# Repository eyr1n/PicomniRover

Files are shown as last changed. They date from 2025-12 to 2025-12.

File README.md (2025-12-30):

# PicomniRover サポートリポジトリ

## 目次

- [これは何？](#これは何)
- [購入するものリスト](#購入するものリスト)
  - [秋月電子通商で購入可能なもの](#秋月電子通商で購入可能なもの)
  - [ロボットショップで購入可能なもの](#ロボットショップで購入可能なもの)
  - [モノタロウで購入可能なもの](#モノタロウで購入可能なもの)
- [3Dプリント部品について](#3dプリント部品について)
- [基板について](#基板について)
- [ライセンス](#ライセンス)

## これは何？

本リポジトリは、コミックマーケット107にて頒布した「やる気出ないんズ 活動報告書 vol.1」内の「かんたん！全方位移動ロボットのつくりかた」にて製作する全方位移動ロボット「PicomniRover」に関する情報をまとめたリポジトリです。

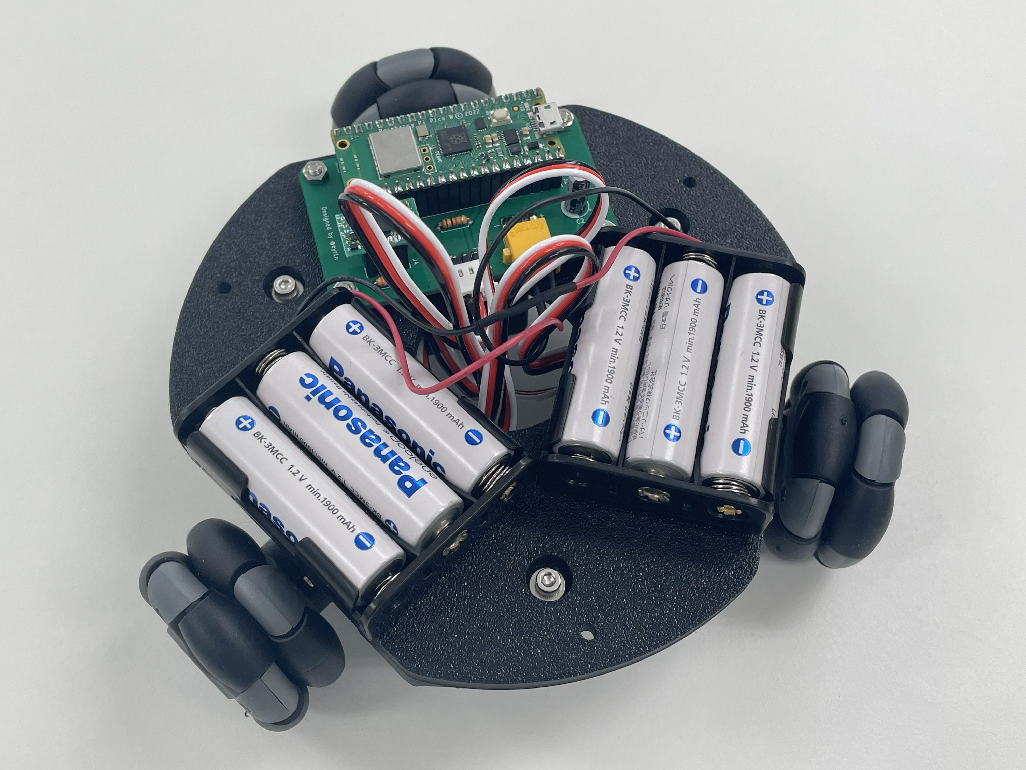
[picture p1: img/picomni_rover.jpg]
PicomniRover


## 購入するものリスト

ここでは、購入する必要のある市販の部品についてまとめます。私が使用した購入先は以下の3つです。

- [秋月電子通商 - https://akizukidenshi.com/](https://akizukidenshi.com/)
- [ロボットショップ(ヴイストン) - https://www.vstone.co.jp/robotshop/](https://www.vstone.co.jp/robotshop/)
- [モノタロウ - https://www.monotaro.com/](https://www.monotaro.com/)

すべてオンライン購入を前提に記載していますが、ねじ類などは近所のホームセンターでも代替可能です。必要に応じて入手しやすい手段を選んでいただければと思います。

また、同人誌内で製作するロボットの動作には、単3形の充電式ニッケル水素電池(公称1.2V)が6本必要です。Panasonic製eneloopやSony製CycleEnergyなど、単3形で公称電圧1.2Vの充電式ニッケル水素電池を用意してください。1.5Vのアルカリ乾電池は使用しないでください。

### 秋月電子通商で購入可能なもの

| 商品名 | 数量(使用数) | 単価(購入単位) | 購入リンク |
| --- | --- | --- | --- |
| Raspberry Pi Pico W | 1個 | ¥1,200 | [リンク](https://akizukidenshi.com/catalog/g/g117947) | 
| BNO055使用 9軸センサーフュージョンモジュールキット/AE-BNO055-BO | 1個 | ¥2,450 | [リンク](https://akizukidenshi.com/catalog/g/g116996) | 
| FEETECHシリアルバスサーボ STS3215 7.4V 14.4kg・cm 1:147 | 3個 | ¥2,780 | [リンク](https://akizukidenshi.com/catalog/g/g131132) | 
| 超高効率DCDCコンバーター(3.3V 0.5A) M78AR033-0.5 | 1個 | ¥380 | [リンク](https://akizukidenshi.com/catalog/g/g107178) | 
| 電池ボックス 単3×3本 リード線/BH-331-3A | 2個 | ¥70 | [リンク](https://akizukidenshi.com/catalog/g/g102667) | 
| XT30コネクター オス 基板取付用 XT30PW-M | 1個 | ¥70 | [リンク](https://akizukidenshi.com/catalog/g/g117949) | 
| XT30コネクター メス XT30U-F | 1個 | ¥50 | [リンク](https://akizukidenshi.com/catalog/g/g117950) | 
| Pch MOSFET 2SJ496TZ-E (60V 5A) | 1個 | ¥90 | [リンク](https://akizukidenshi.com/catalog/g/g109040) | 
| 電解コンデンサー 100μF 25V 105℃ ルビコンPX/25PX100MEFC5X11 | 1個 | ¥10 | [リンク](https://akizukidenshi.com/catalog/g/g117877) | 
| 積層セラミックコンデンサー 3.3μF 50V X7R 5mm/RDER71H335K3K1H03B | 1個 | ¥50 | [リンク](https://akizukidenshi.com/catalog/g/g108153) | 
| カーボン抵抗(炭素皮膜抵抗) 1/4W 1kΩ/CF25J1KB | 1本 (100本/袋) | ¥100 | [リンク](https://akizukidenshi.com/catalog/g/g125102) | 
| カーボン抵抗(炭素皮膜抵抗) 1/4W 3.3kΩ/CF25J3K3B | 2本 (100本/袋) | ¥140 | [リンク](https://akizukidenshi.com/catalog/g/g125332) | 
| ピンヘッダー 1×40 (40P)/PH-1x40SG | 2個 | ¥35 | [リンク](https://akizukidenshi.com/catalog/g/g100167) | 
| ピンヘッダー (L型) 1×6 (6P)/PH-1X6RG(2) | 1個 | ¥10 | [リンク](https://akizukidenshi.com/catalog/g/g105336) | 
| 分割ロングピンソケット 1×42 (42P)/FHU-1x42SG | 2個 | ¥80 | [リンク](https://akizukidenshi.com/catalog/g/g105779) | 
| 合計 |  | ¥13,260 |  | 

### ロボットショップで購入可能なもの

| 商品名 | 数量(使用数) | 単価(購入単位) | 購入リンク |
| --- | --- | --- | --- |
| 48mmオムニホイール(六角ハブ対応)(14038) | 3個 | ¥715 | [リンク](https://www.vstone.co.jp/robotshop/index.php?main_page=product_info&products_id=5180) | 
| 合計 |  | ¥2,145 |  | 

### モノタロウで購入可能なもの

| 商品名 | 数量(使用数) | 単価(購入単位) | 購入リンク |
| --- | --- | --- | --- |
| 六角穴付ボルト(ステンレス) 全ねじ M3×10mm | 6個 | ¥681 (55個/袋) | [リンク](https://www.monotaro.com/p/2901/7714/) | 
| 六角穴付ボルト(ステンレス) 全ねじ M3×12mm | 4個 | ¥802 (54個/袋) | [リンク](https://www.monotaro.com/p/2901/7723/) | 
| 六角穴付ボルト(ステンレス) 全ねじ M3×30mm | 3個 | ¥659 (25個/袋) | [リンク](https://www.monotaro.com/p/6891/0652/) | 
| 六角ナット1種 ステンレス M3 | 14個 | ¥175 (50個/袋) | [リンク](https://www.monotaro.com/p/2876/3448/) | 
| 平ワッシャー ステンレス M3×8×0.5 | 6個 | ¥99 (50個/袋) | [リンク](https://www.monotaro.com/p/2876/4114/) | 
| 合計 |  | ¥2,416 |  | 

## 3Dプリント部品について

ここでは、3Dプリンターで印刷する必要のある部品についてまとめます。ここで紹介する部品は、C107にて頒布した「ロボット部品セット」を購入した場合、印刷不要です。

印刷に使用した環境は以下の通りです。

- プリンター: Bambu Lab A1 mini
- ノズル径: 0.4mm
- プリセット: 0.20mm Standard @BBL A1M
- フィラメント: eSUN PLA+

| 部品名 | STEPファイル | 数量 | 備考 |
| --- | --- | --- | --- |
| ボディー | [STEP/body.step](STEP/body.step) | 1個 | 1層目のみ30mm/sで印刷 | 
| モーター固定具 | [STEP/motor_bracket.step](STEP/motor_bracket.step) | 3個 |  | 
| ホイール固定具1 | [STEP/wheel_mount1.step](STEP/wheel_mount1.step) | 3個 |  | 
| ホイール固定具2 | [STEP/wheel_mount2.step](STEP/wheel_mount2.step) | 3個 |  | 
| 基板スペーサー | [STEP/pcb_spacer.step](STEP/pcb_spacer.step) | 4個 |  | 

## 基板について

同人誌内で使用するシールド基板は KiCad 9.0.6 で設計し、JLCPCB に製造を発注しました。

プロジェクトファイル一式は [KiCad/PicomniRover](KiCad/PicomniRover) (`PicomniRover.kicad_pro` / `.kicad_pcb` / `.kicad_sch`) にあり、製造用ガーバーデータは [KiCad/PicomniRover/jlcpcb/production_files/GERBER-PicomniRover.zip](KiCad/PicomniRover/jlcpcb/production_files/GERBER-PicomniRover.zip) にまとめています。

回路図は以下の通りです。

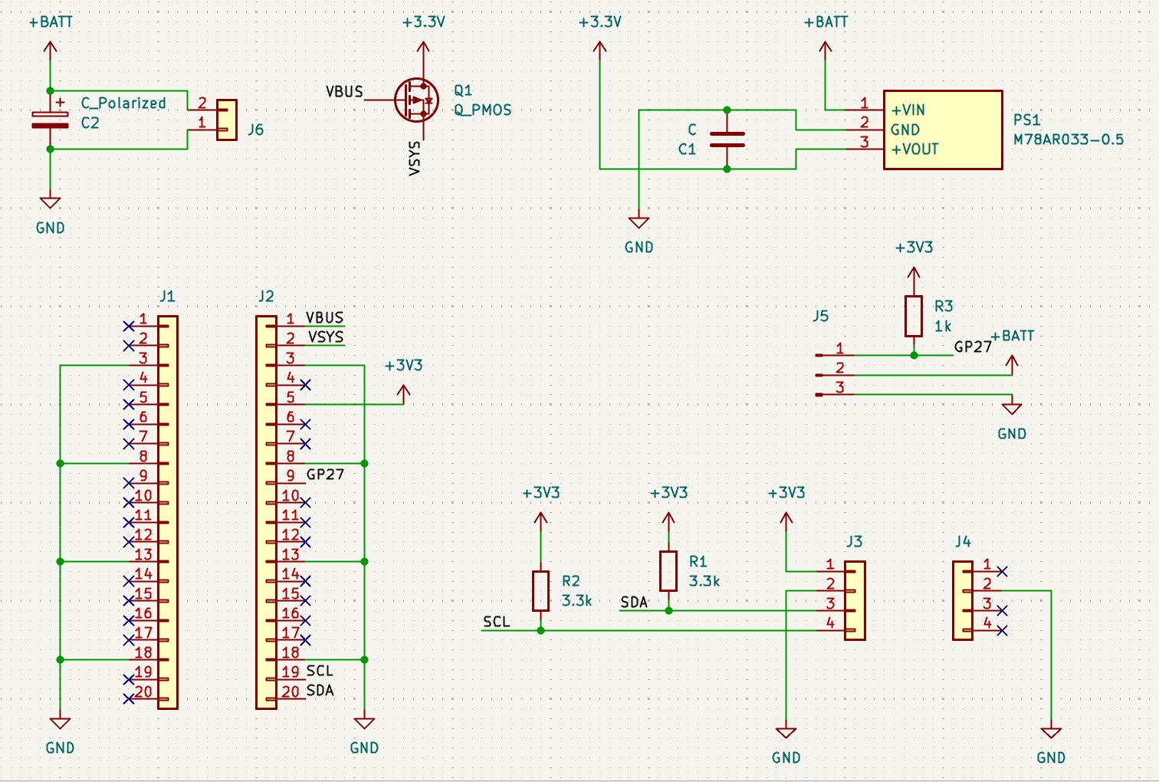
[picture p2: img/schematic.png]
回路図


## ライセンス

MIT ライセンス

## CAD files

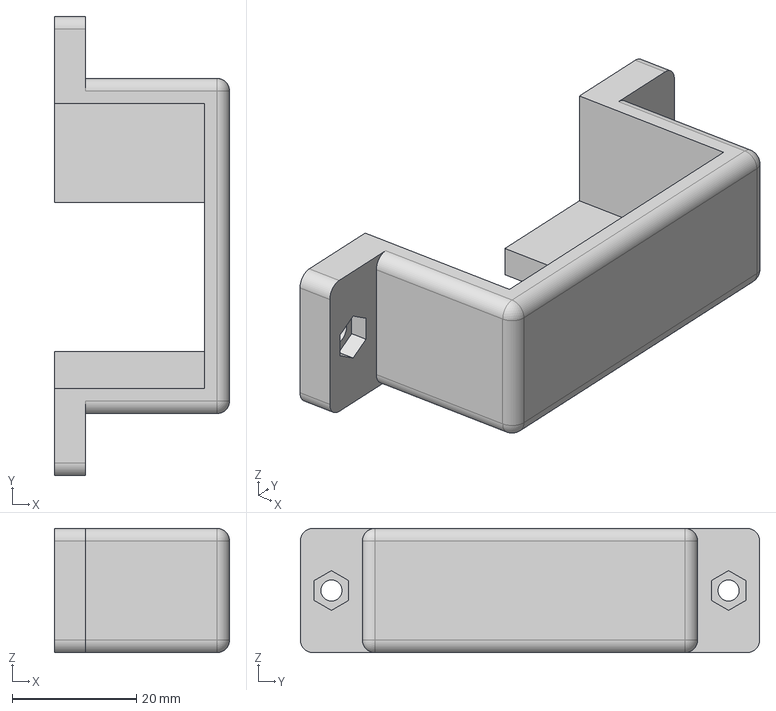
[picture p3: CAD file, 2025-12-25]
STEP/motor_bracket.step
28.2 x 74.0 x 20.0 mm

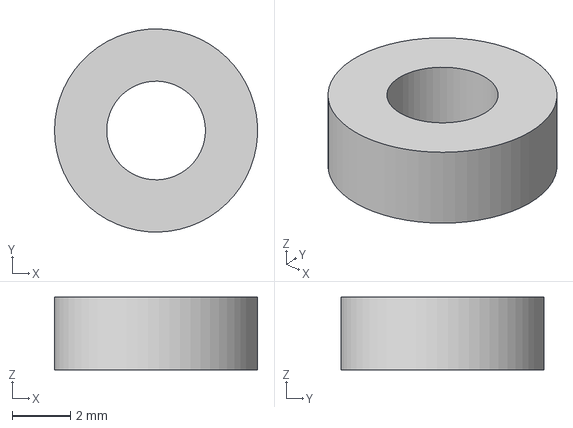
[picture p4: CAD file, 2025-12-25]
STEP/pcb_spacer.step
7.00 x 7.00 x 2.50 mm

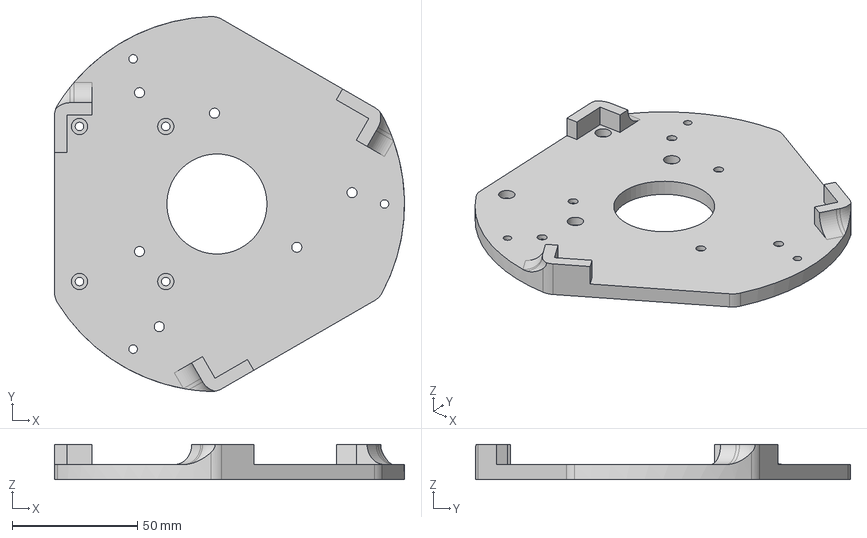
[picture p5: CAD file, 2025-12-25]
STEP/body.step
140.0 x 149.9 x 14.0 mm

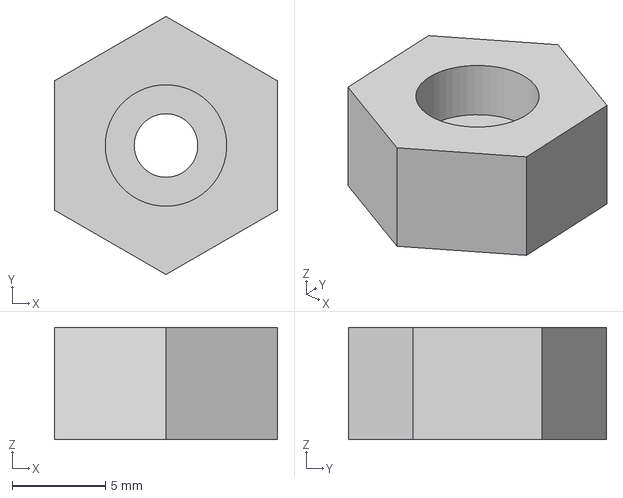
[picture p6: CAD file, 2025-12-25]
STEP/wheel_mount2.step
12.0 x 13.8 x 6.00 mm

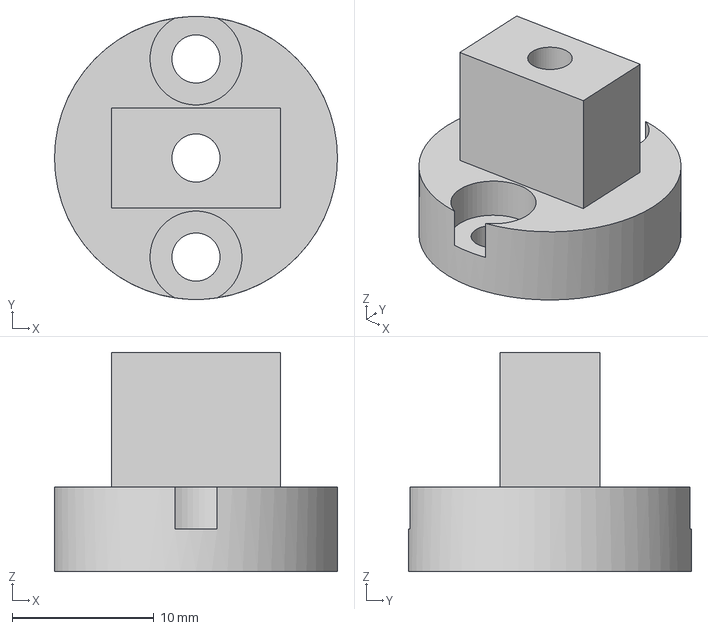
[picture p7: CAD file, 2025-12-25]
STEP/wheel_mount1.step
20.0 x 20.0 x 15.5 mm

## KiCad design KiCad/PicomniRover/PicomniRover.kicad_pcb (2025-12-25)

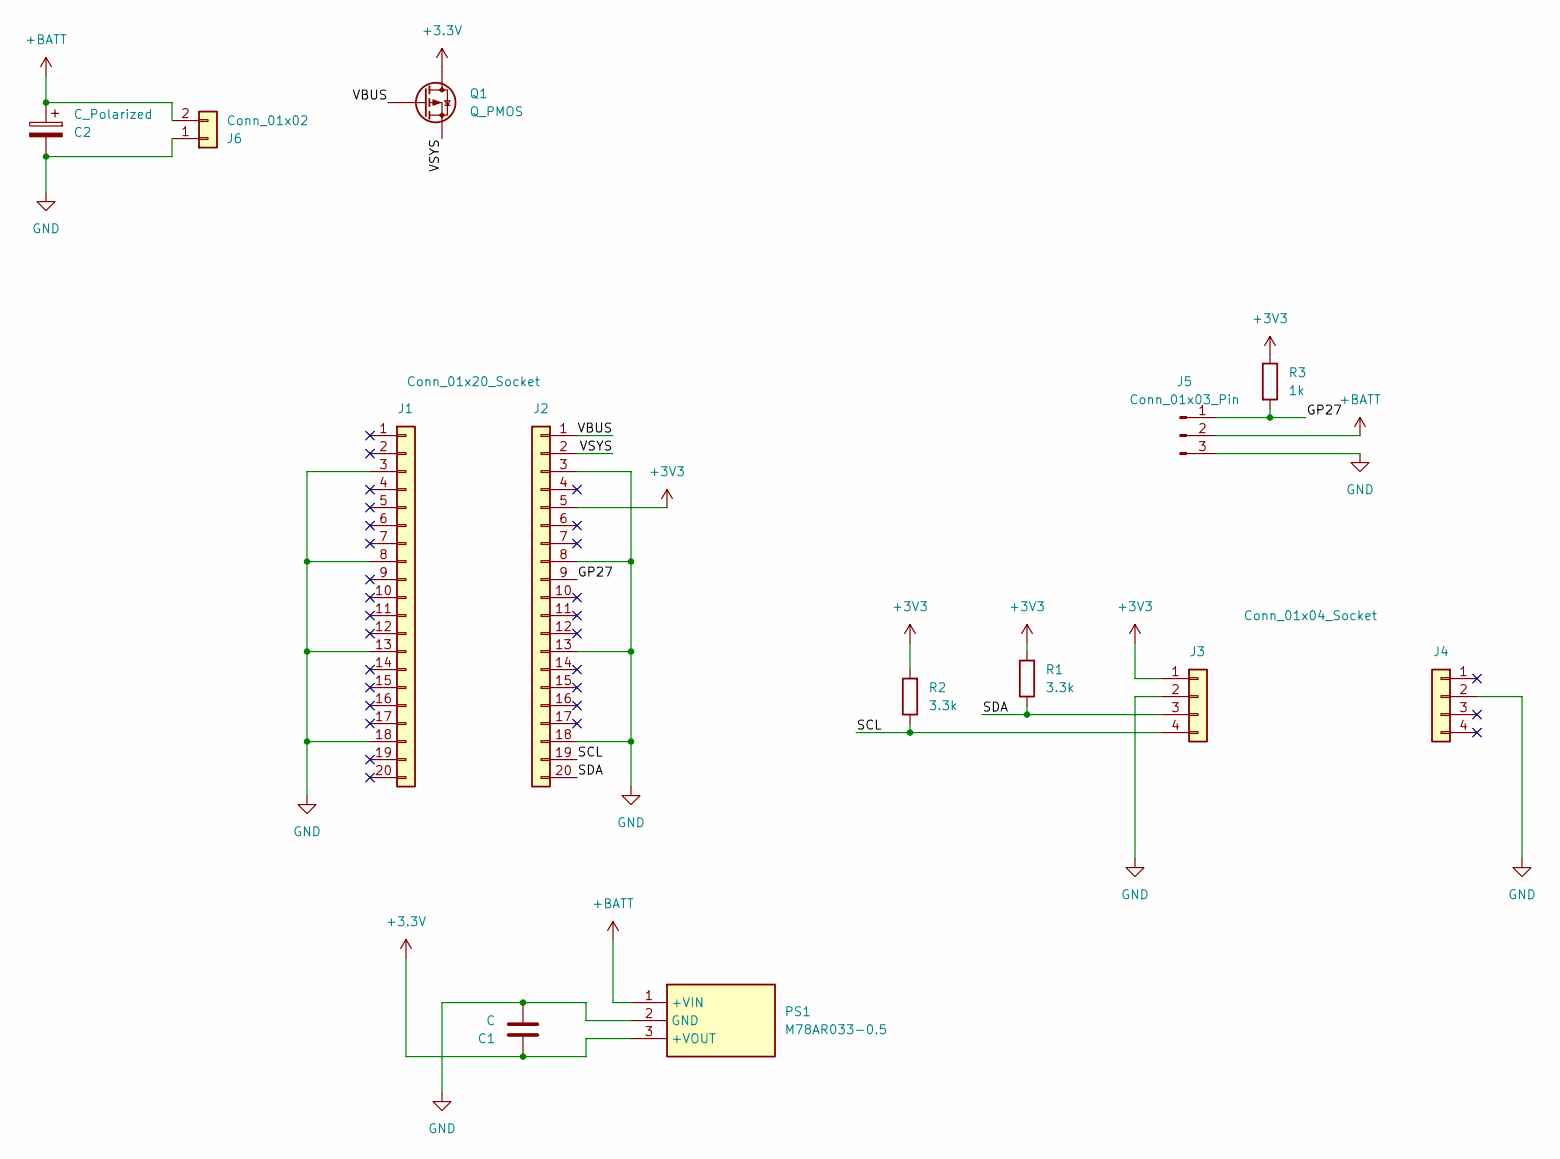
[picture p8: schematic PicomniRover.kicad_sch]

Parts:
C1: C; C_Disc_D5.0mm_W2.5mm_P5.00mm
C2: C_Polarized; CP_Radial_D6.3mm_P2.50mm
J1, J2: Conn_01x20_Socket; PinSocket_1x20_P2.54mm_Vertical
J3, J4: Conn_01x04_Socket; PinSocket_1x04_P2.54mm_Vertical
J5: Conn_01x03_Pin; PinHeader_1x03_P2.54mm_Horizontal
J6: Conn_01x02; AMASS_XT30PW-M_1x02_P2.50mm_Horizontal
PS1: M78AR033-0.5; M78AR03305; Manufacturer_Part_Number M78AR033-0.5
Q1: Q_PMOS; TO-92_Inline_Wide
R1, R2: 3.3k; R_Axial_DIN0207_L6.3mm_D2.5mm_P7.62mm_Horizontal
R3: 1k; R_Axial_DIN0207_L6.3mm_D2.5mm_P7.62mm_Horizontal

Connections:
+3.3V: C1.1, PS1.3 (+VOUT), Q1.2 (D)
+3V3: J2.5, J3.1, R1.2, R2.2, R3.1
+BATT: C2.1, J5.2, J6.2, PS1.1 (+VIN)
/GP27: J2.9, J5.1, R3.2
/SCL: J2.19, J3.4, R2.1
/SDA: J2.20, J3.3, R1.1
/VBUS: J2.1, Q1.3 (G)
/VSYS: J2.2, Q1.1 (S)
GND: C1.2, C2.2, J1.3, J1.8, J1.13, J1.18, J2.3, J2.8, J2.13, J2.18, J3.2, J4.2, J5.3, J6.1, PS1.2 (GND)

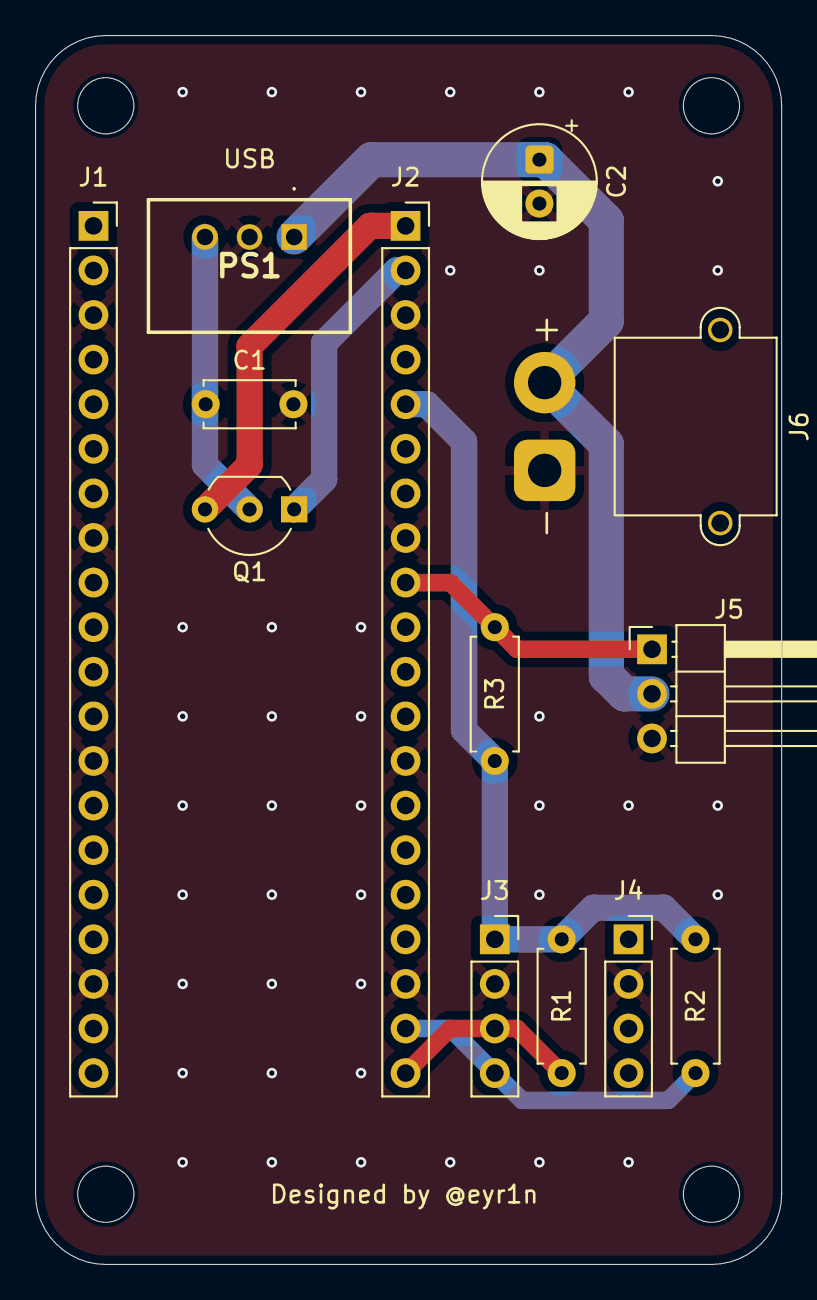
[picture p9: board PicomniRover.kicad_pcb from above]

Board: 2 copper layers, 42.5 x 70.0 mm, 13 parts (0 on the bottom side), 9 nets.

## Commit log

2025-12-30 いろいろ書いた
2025-12-30 電池について
